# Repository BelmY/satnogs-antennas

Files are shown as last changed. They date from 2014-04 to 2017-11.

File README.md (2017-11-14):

# SatNOGS Antennas

Antennas for SatNOGS project

More information can be found in our [documentation](https://satnogs.org/documentation/hardware/).

## What's here?

### Helical antenna designs

* `Helical/UHC lhcp-version_1` is version 1 of our Helical antenna design.  It's
  a left-hand circularly polarized (LHCP) antenna, and requires only
  3D-printed parts (no CNC milling or laser-cutting required).

* `Helical/UHF-434-8-version_4` is version 4 of our Helical antenna design, an
  8-turn Helix that can be made in either left- or right-hand
  circularly polarized (RHCP) configurations.  It requires a laser cutter or
  water jet cutter for the plexiglass/polycarbonate supports, but is
  more rigid than version 1.

* `Helical/UHF-435-8-version_5` is version 5 of the Helical antenna
  design; it comes in RHCP configuration.  The supports are made from
  aluminum, and will require a drill press.

## License

&copy; 2014-2015 [Libre Space Foundation](http://librespacefoundation.org).

Licensed under the [CERN OHLv1.2](LICENSE).

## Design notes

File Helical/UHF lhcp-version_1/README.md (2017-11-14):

Documentation
====
Documentation and step by step building guide can be found in our [OHAI guide](https://ohai.satnogs.org/project/helical-antenna-v1/hardware/).

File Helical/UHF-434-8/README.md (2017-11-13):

# Helical Antenna v4

What's here:

* Summary files for RHCP antenna in stl and dxf format
  * Helical-434-8-RHCP.stl
  * Helical-434-8-RHCP.dxf

* Summary files for LHCP antenna in stl and dxf format
  * Helical-434-8-LHCP.stl
  * Helical-434-8-LHCP.dxf

* Printable blueprint file for RHCP in dxf and pdf format
  * Helical-434-RHCP-printBase.dxf
  * Helical-434-RHCP-printBase.pdf

* Printable blueprint file for LHCP in dxf and pdf format
  * Helical-434-LHCP-printBase.dxf
  * Helical-434-LHCP-printBase.pdf

* 6 radial base file for plexiglass or polycarbonate base in dxf and pdf format
  * Helical-434-6radialBase.dxf
  * Helical-434-6radialBase.pdf

* Plexiglass or polycarbonate triangular connector files
  * Helical-434-Triangle.dxf
  * Helical-434-Triangle.pdf

* Cooper matching triagle
  * Helical-434-CooperTriangle.dxf
  * Helical-434-CooperTriangle.pdf

* Dimensions table
  * Helical-434-8.xls

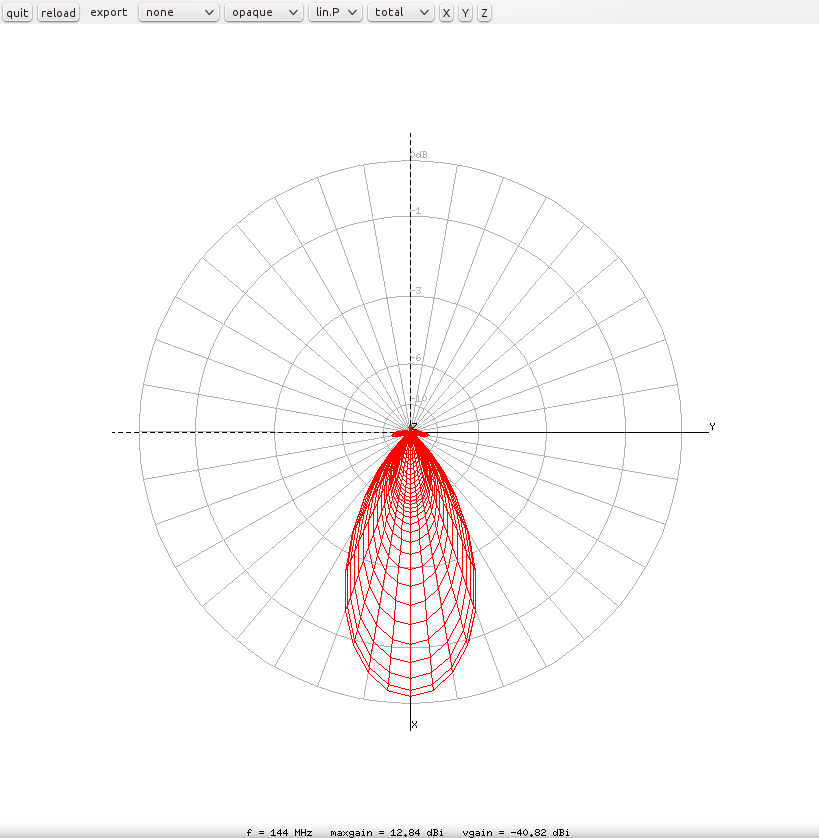
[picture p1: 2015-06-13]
NEC/SatNOGS 6-element - Radiation pattern.png

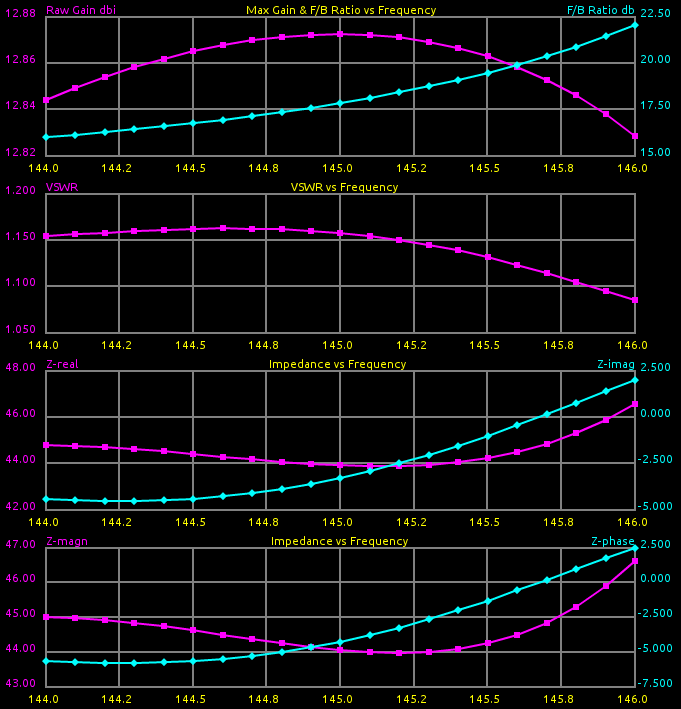
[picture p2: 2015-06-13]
NEC/SatNOGS 6-element - Gain_SWR_Impedance.png

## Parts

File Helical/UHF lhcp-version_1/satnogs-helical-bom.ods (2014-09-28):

Category | Description | Source | Qty | UOM | Estimated Price per Unit | Total Price | Comments
Mechanical | Galvanized Steel Wire 2mm |  | 10 | m | 0.2 | 2
Mechanical | Φ16 PVC Pipe |  | 6 | m | 1 | 6 | Condur Heavy Type
Mechanical | Galvanized Steel Grid 0.5x0.5'' 1mm |  | 0.16 | sqm | 8 | 1.28
Mechanical | Brass metal sheet 1.2mm |  | 0.45 | kg | 9 | 4.05 | We only need an orthogonal metal triangle of 204x41mm dimensions
Mechanical | M3 x 10mm |  | 0.02 | ea | 2 | 0.04
Mechanical | N-type Connector for case |  | 1 | ea | 4 | 4
Mechanical | M3 nut |  | 2 | ea | 0.01 | 0.02
Mechanical | M4 washer |  | 2 | ea | 0.02 | 0.04 | Enough big to be bigger than the grid square
Printed | T-Connector | Helix437-8r3-T.stl | 9 | ea | 0 | 0 | 3D printed, you can also use a finer design (check drawing)
Printed | Y-Connector | Helix437-8r3-Y.stl | 2 | ea | 0 | 0 | 3D printed, you can also use a finer design (check drawing)
Printed | YO-Connector | Helix437-8r3-YO.stl | 1 | ea | 0 | 0 | 3D printed, you can also use a finer design (check drawing)
 |  |  |  |  |  | 17.43

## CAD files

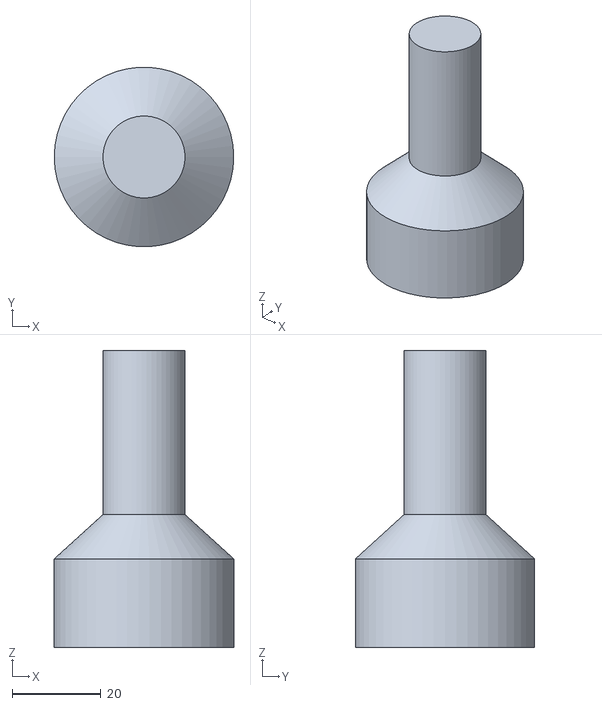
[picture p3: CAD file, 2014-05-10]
Turnstile/SatNOGS-turnstile-mount.stl
40.5 x 40.4 x 67.0

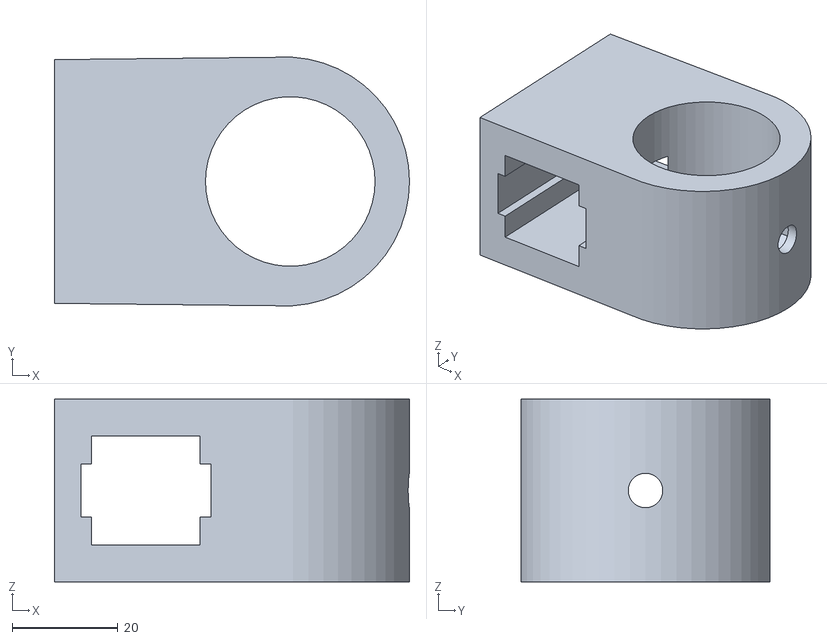
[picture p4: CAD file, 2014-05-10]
Yagi/Cross-Yagi-UHF-v1/satnogs-antenna-axis-mount-v2.stl
67.0 x 46.9 x 34.5

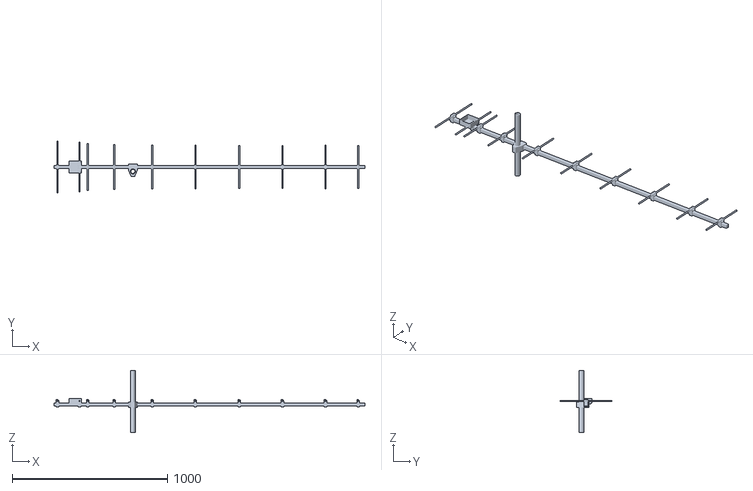
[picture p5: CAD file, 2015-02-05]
Yagi/Yagi-UHF-v1/435MHz-10EL8mm-2m-50-Ohm-Yagi.stl
2006.0 x 333.0 x 400.0

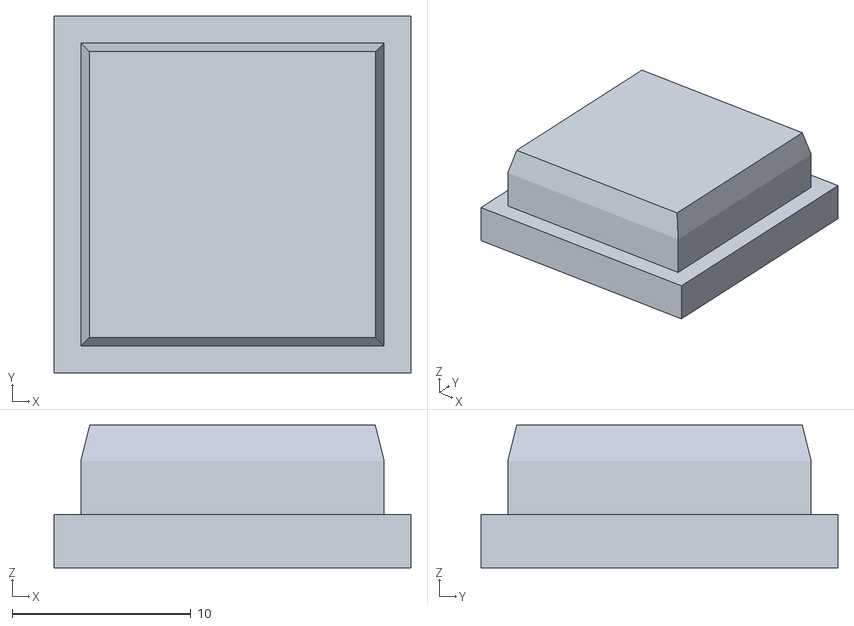
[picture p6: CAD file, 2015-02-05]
Yagi/Yagi-VHF-v3/Boom-cap.stl
20.0 x 20.0 x 8.00

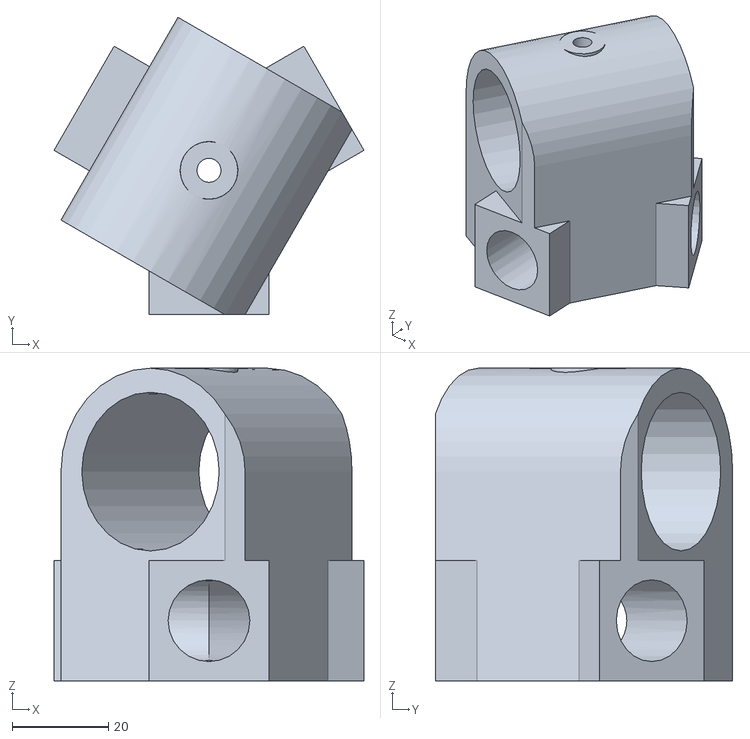
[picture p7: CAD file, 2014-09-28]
Helical/UHF lhcp-version_1/Helix437-8r3-YO.stl
64.5 x 61.8 x 65.0

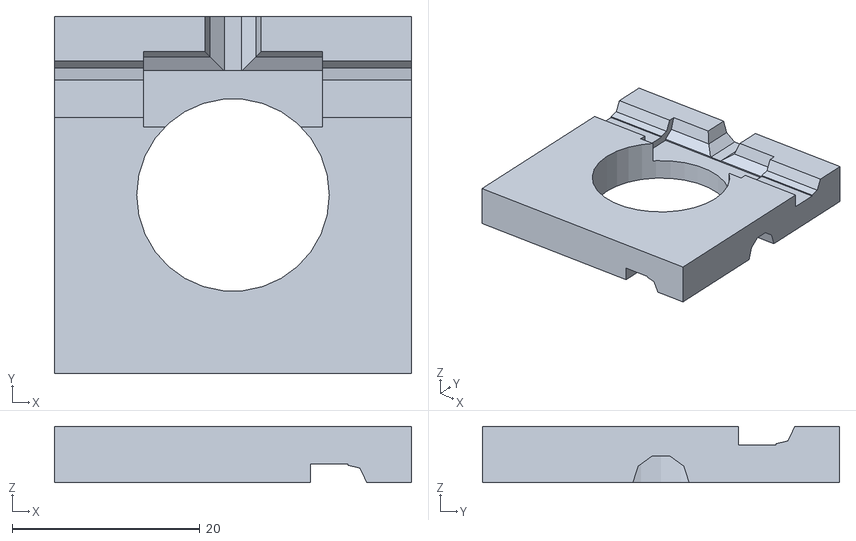
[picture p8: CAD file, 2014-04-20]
Yagi/Cross-Yagi-UHF-v1/satnogs-radiator-holder-middle.stl
38.0 x 38.0 x 6.00

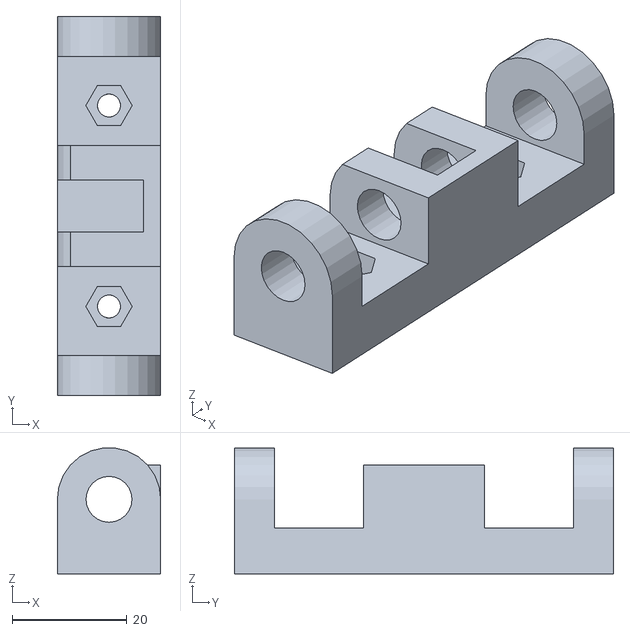
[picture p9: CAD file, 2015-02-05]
Yagi/Yagi-UHF-v1/El-middle435.stl
18.0 x 66.0 x 21.9

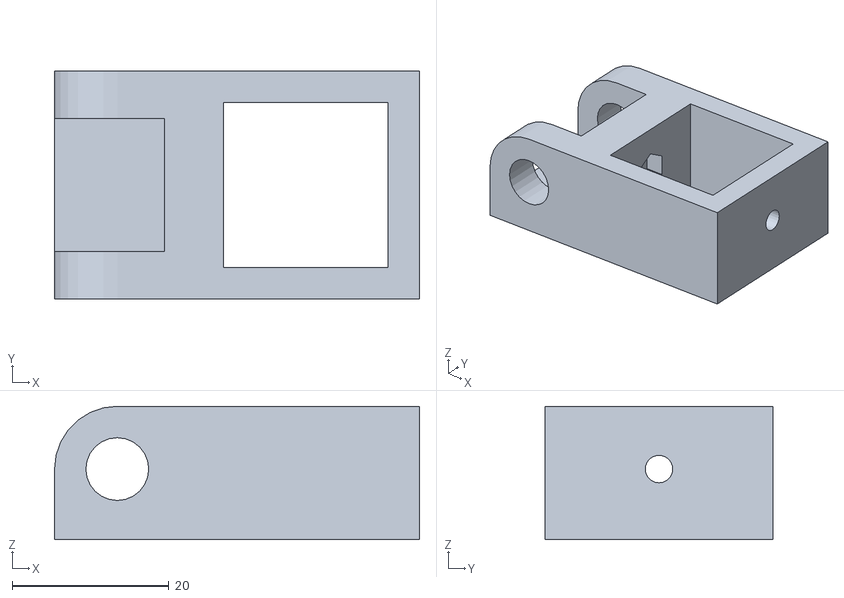
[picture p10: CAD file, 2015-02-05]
Yagi/Yagi-VHF-v3/El-conn.stl
46.5 x 29.0 x 17.0

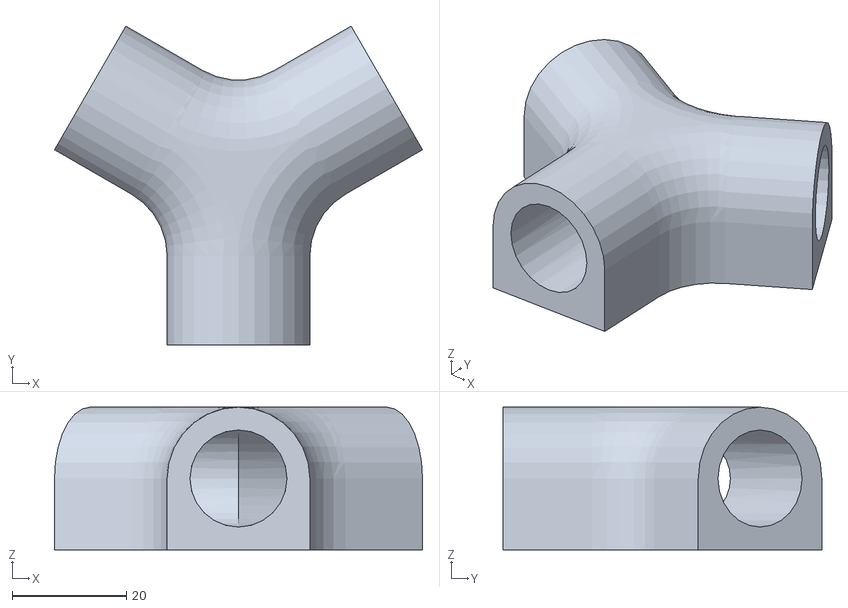
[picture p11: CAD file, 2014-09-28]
Helical/UHF lhcp-version_1/Helix437-8r3-Y.stl
64.5 x 55.8 x 25.0

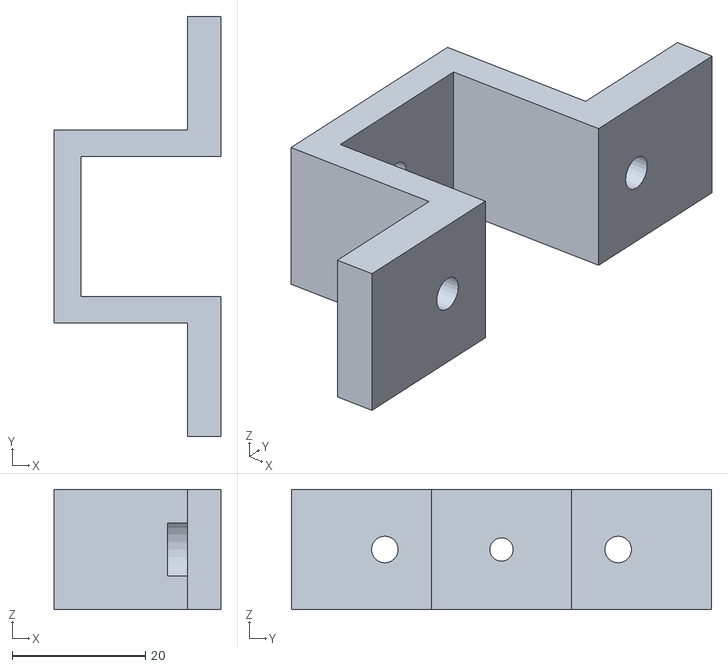
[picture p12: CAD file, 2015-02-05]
Yagi/Yagi-UHF-v1/omega435.stl
25.0 x 63.0 x 18.0

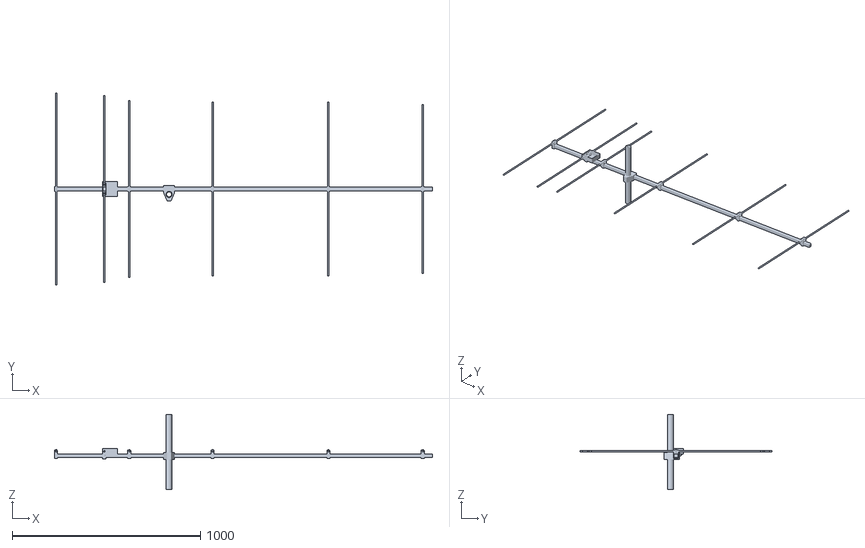
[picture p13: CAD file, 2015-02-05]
Yagi/Yagi-VHF-v3/145MHz-6EL8mm-2m-50-Ohm-Yagi.stl
2009.0 x 1020.0 x 400.0

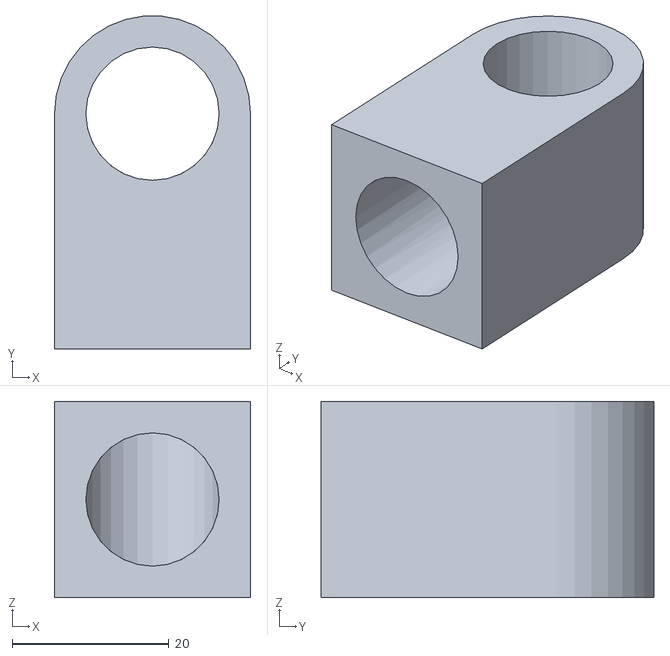
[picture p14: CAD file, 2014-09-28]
Helical/UHF lhcp-version_1/Helix437-8r3-T.stl
25.0 x 42.4 x 25.0

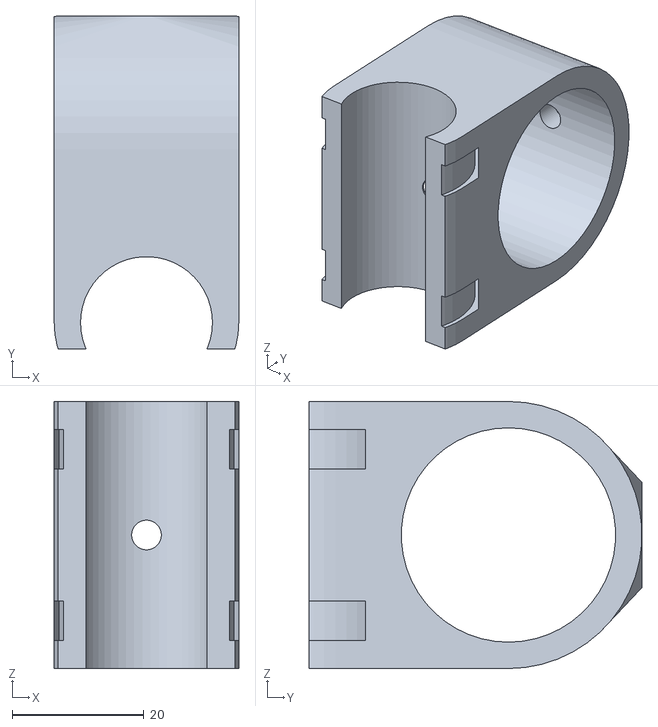
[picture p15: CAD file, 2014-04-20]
Yagi/Cross-Yagi-UHF-v1/satnogs-antenna-axis-mount-single-pole.stl
28.0 x 50.5 x 40.5

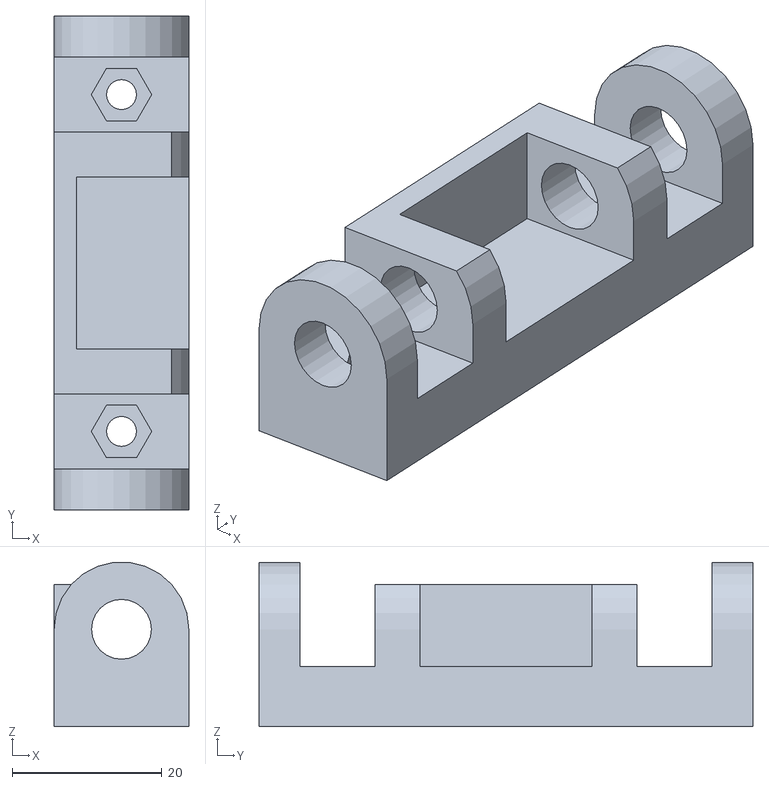
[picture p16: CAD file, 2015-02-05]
Yagi/Yagi-VHF-v3/El-middle145.stl
18.0 x 66.0 x 21.9

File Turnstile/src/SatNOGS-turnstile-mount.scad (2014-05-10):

// SatNOGS Turnstile antenna mount

$fn=50;

// Variables
i_b = 32.5; //Inner Bottom width
o_u = 18.5; //Outer Upper width
t_h = 10; //Transitional height

// Main model

module mount(){
	difference(){
		union(){
			translate([0,0,-10])
				cylinder(d=i_b+8, h=20, center=true);
			translate([0,0,t_h/2])
				cylinder(d1=i_b+8, d2=o_u, h=t_h, center=true);
			translate([0,0,t_h+(o_u*2)/2])
				cylinder(d=o_u, h=o_u*2, center=true);
		}
		translate([0,0,-11])
			cylinder(d=i_b, h=22, center=true);
	}
}

mount();

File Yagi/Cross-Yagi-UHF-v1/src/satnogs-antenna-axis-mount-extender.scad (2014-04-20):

// Antenna to axis mount
// Satnogs Project 2014 MPL2.0 http://satnogs.org

$fn=50;

mast_1 = 32;		 // Axis mast diameter
mast_2 = 20;		 // Antenna mast diameter
offset = 8;			 // Extra width of mount
tireup_w = 6; 		 // Width of tireup
tireup_h = 1.5;	 // Height of tireup
washer = 16;		 // Washer diameter
bolt = 4;			 // Bolt for antenna mast


module axises() {
	translate([0,(mast_1+mast_2)/2-mast_1/2,0])
		rotate([0,90,0])
			cylinder(h=mast_2+offset+1, d=mast_1, center=true);
	translate([0,-(mast_1+mast_2)/2+mast_2/2,0])
		cylinder(h=mast_1+offset+1, d=mast_2, center=true);
	// Bolt for antenna mast cylinder
	translate([0,(mast_1+mast_2)/2-mast_1/2,0])
		cylinder(h=mast_1+offset+1, d=bolt, center=true);
}

module axises_outer() {
	translate([0,(mast_1+mast_2)/2-mast_1/2,0])
		rotate([0,90,0])
			cylinder(h=mast_2+offset, d=mast_1+offset, center=true);
	translate([0,-(mast_1+mast_2)/2+mast_2/2,0])
		cylinder(h=mast_1+offset, d=mast_2+offset, center=true);
	// Outer washer stud
	translate([0,(mast_1+mast_2)/2-mast_1/2,0])
		cylinder(h=mast_1+offset, d=washer, center=true);
}

module tire_up() {
	difference() {
		cylinder(h=tireup_w,d=mast_2+offset+tireup_h,center=true);
		cylinder(h=tireup_w,d=mast_2+offset-tireup_h,center=true);
	}
}

module cut() {
	translate([0,-(mast_1+mast_2)/2,0])
		cube([offset*5,offset*1.5,mast_1+offset*4],center=true);
}

module main_connector() {
	difference() {
		hull() {
			axises_outer();
		}
		axises();
		mirror([0,0,1]) {
			translate([0,-(mast_1+mast_2)/2+mast_2/2,(2*mast_1)/5])
				tire_up();
		}
		translate([0,-(mast_1+mast_2)/2+mast_2/2,(2*mast_1)/5])
			tire_up();
		cut();
	}
}

module extender() {
	difference() {
		translate([mast_1/2-offset/2,-mast_2*2,-mast_1/2-offset/4])
			cube([offset/2,mast_1*2,offset/2],center=true);
		translate([mast_1/2-offset/2,-mast_1*2-4,-mast_1/2-offset/4])
			cylinder(d=3,offset/2,center=true);
	}
}

difference() {
	union() {
		main_connector();
		extender();
	}
}

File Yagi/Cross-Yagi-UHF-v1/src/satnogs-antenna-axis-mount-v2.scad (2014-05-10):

// SatNOGS Yagi v2 Axis mount

//$fn = 20;

include <cyl_head_bolt.scad>;

// Variables

axis = 32; //Axis diameter
mast = 20.5; //Yagi width
w = 7; 	  //Mount wall width

module mount_outer(){
	union(){
		translate([axis/2+1,0,0])
			cylinder(d=axis+2*w,h=mast+2*w,center=true);
		translate([-mast/2,0,0])
			cube([mast+2*w,axis+2*w,mast+2*w],center=true);
	}
}

module mount_inner(){
	union(){
		translate([axis/2+1,0,0])
			cylinder(d=axis,h=mast+2*w+1,center=true);
		translate([-mast/2,0,0])
			cube([mast,axis+2*w+1,mast],center=true);
	}
}

module nutsbolts(){
	translate([-mast+1,0,0])
		rotate([0,90,0])
			nutcatch_parallel("M6", l=6);
	translate([-mast,0,0])
		rotate([0,90,0])
			cylinder(r=3.25,h=15,center=true);
	translate([axis+4,0,0])
		rotate([0,90,0])
			nutcatch_parallel("M6", l=8);
	translate([axis,0,0])
		rotate([0,90,0])
			cylinder(r=3.25,h=15,center=true);
}

module nipple_rail(){
	translate([-mast,0,0])
		cube([4,axis+2*w+1,10],center=true);
	cube([4,axis+2*w+1,10],center=true);
}

difference() {
	hull() {
		mount_outer();
	}
	mount_inner();
	nutsbolts();
	nipple_rail();
}

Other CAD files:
Helical/UHF lhcp-version_1/Helix437-8r3.dwg
Yagi/Yagi-UHF-v1/pipe-conn.stl
Yagi/Cross-Yagi-UHF-v1/src/satnogs-antenna-axis-mount-single-pole.scad
Helical/UHF lhcp-version_1/old/Helix437-8r1.dwg
Helical/UHF lhcp-version_1/old/Helix437-8r2.dwg
Helical/UHF-434-8-version_4/Helical-434-6radialBase.dxf
Helical/UHF-434-8-version_4/Helical-434-CooperTriangle.dxf
Helical/UHF-434-8-version_4/Helical-434-LHCP-printBase.dxf
Helical/UHF-434-8-version_4/Helical-434-RHCP-printBase.dxf
Helical/UHF-434-8-version_4/Helical-434-Triangle.dxf
Yagi/Cross-Yagi-UHF-v1/satnogs-antenna-axis-mount.stl
Yagi/Cross-Yagi-UHF-v1/satnogs-t-connector.stl
Yagi/Cross-Yagi-UHF-v1/satnogs-yagi-holder-4.5mm.stl
Yagi/Cross-Yagi-UHF-v1/satnogs-yagi-holder-4.stl
Yagi/Cross-Yagi-UHF-v1/satnogs-yagi-holder-5mm.stl
Yagi/Cross-Yagi-UHF-v1/satnogs-yagi-holder.stl
Yagi/Cross-Yagi-UHF-v1/src/satnogs-antenna-axis-mount.scad
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

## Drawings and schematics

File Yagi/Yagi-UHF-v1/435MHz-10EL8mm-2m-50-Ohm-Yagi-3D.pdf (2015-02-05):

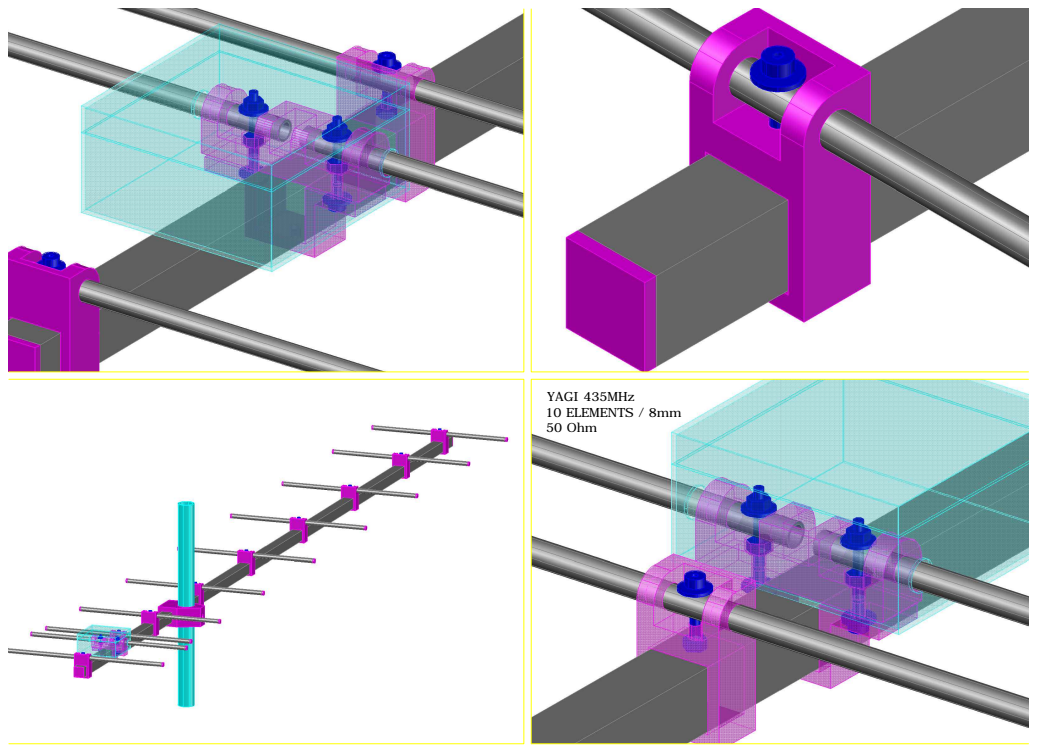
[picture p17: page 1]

YAGI 435MHz 10 ELEMENTS / 8mm 50 Ohm

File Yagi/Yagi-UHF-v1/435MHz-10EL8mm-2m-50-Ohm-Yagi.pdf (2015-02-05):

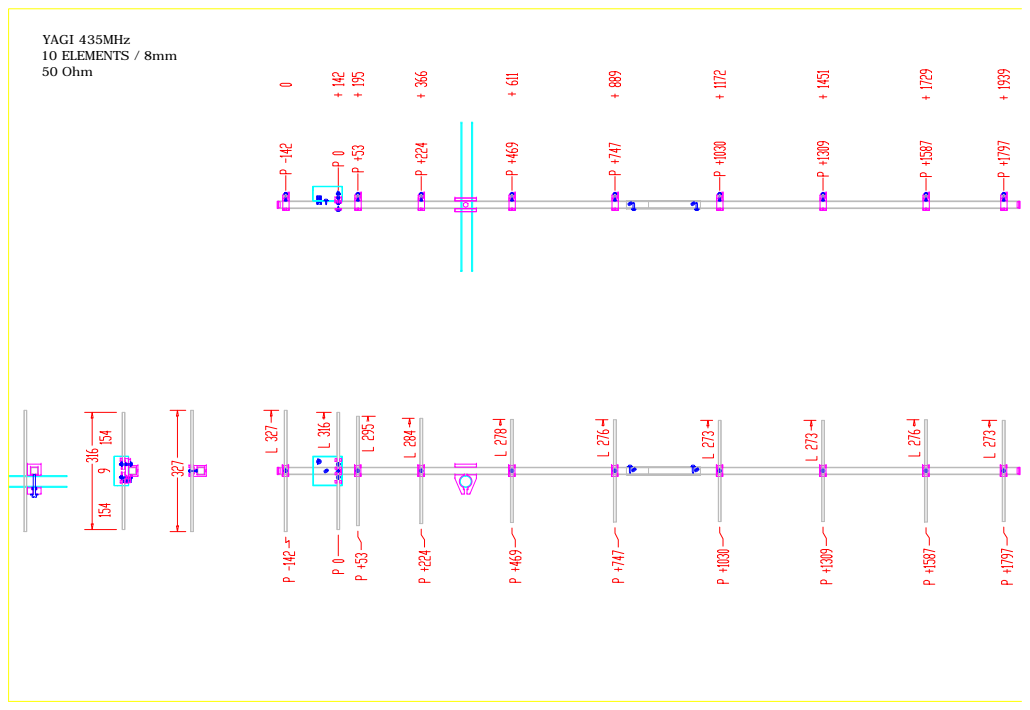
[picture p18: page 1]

YAGI 435MHz 10 ELEMENTS / 8mm 50 Ohm

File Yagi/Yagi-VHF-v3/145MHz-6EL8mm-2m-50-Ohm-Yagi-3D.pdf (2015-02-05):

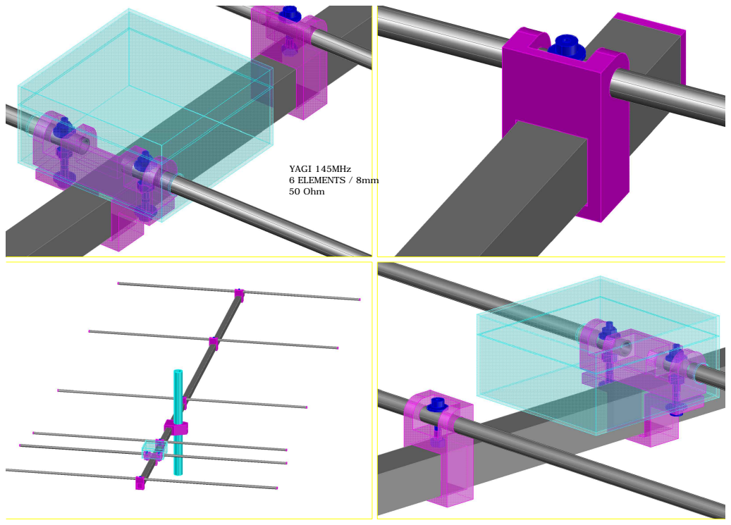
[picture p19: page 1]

YAGI 145MHz 6 ELEMENTS / 8mm 50 Ohm

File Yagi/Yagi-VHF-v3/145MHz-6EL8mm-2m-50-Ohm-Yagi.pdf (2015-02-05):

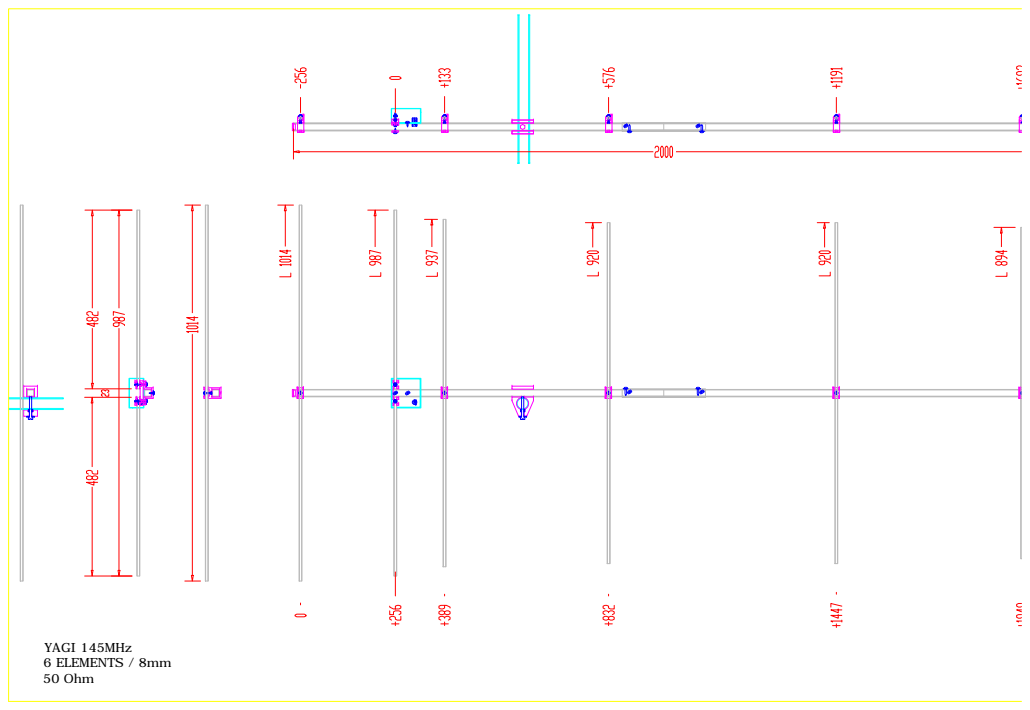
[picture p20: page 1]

YAGI 145MHz 6 ELEMENTS / 8mm 50 Ohm

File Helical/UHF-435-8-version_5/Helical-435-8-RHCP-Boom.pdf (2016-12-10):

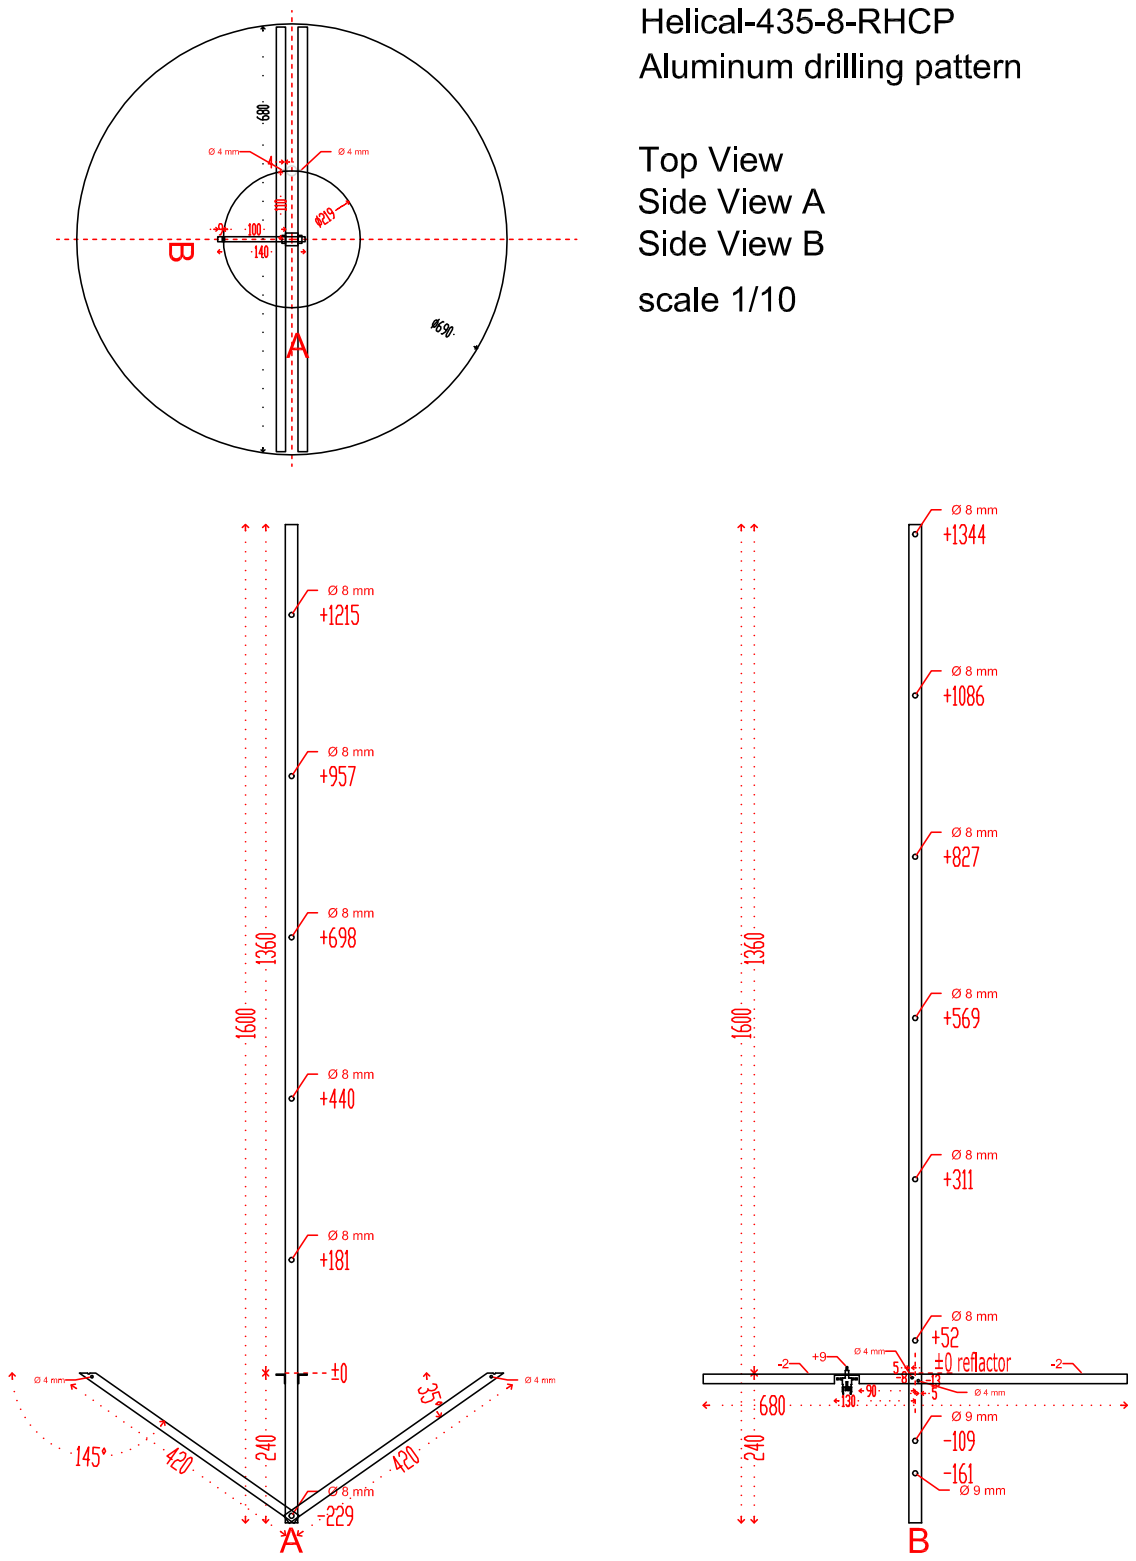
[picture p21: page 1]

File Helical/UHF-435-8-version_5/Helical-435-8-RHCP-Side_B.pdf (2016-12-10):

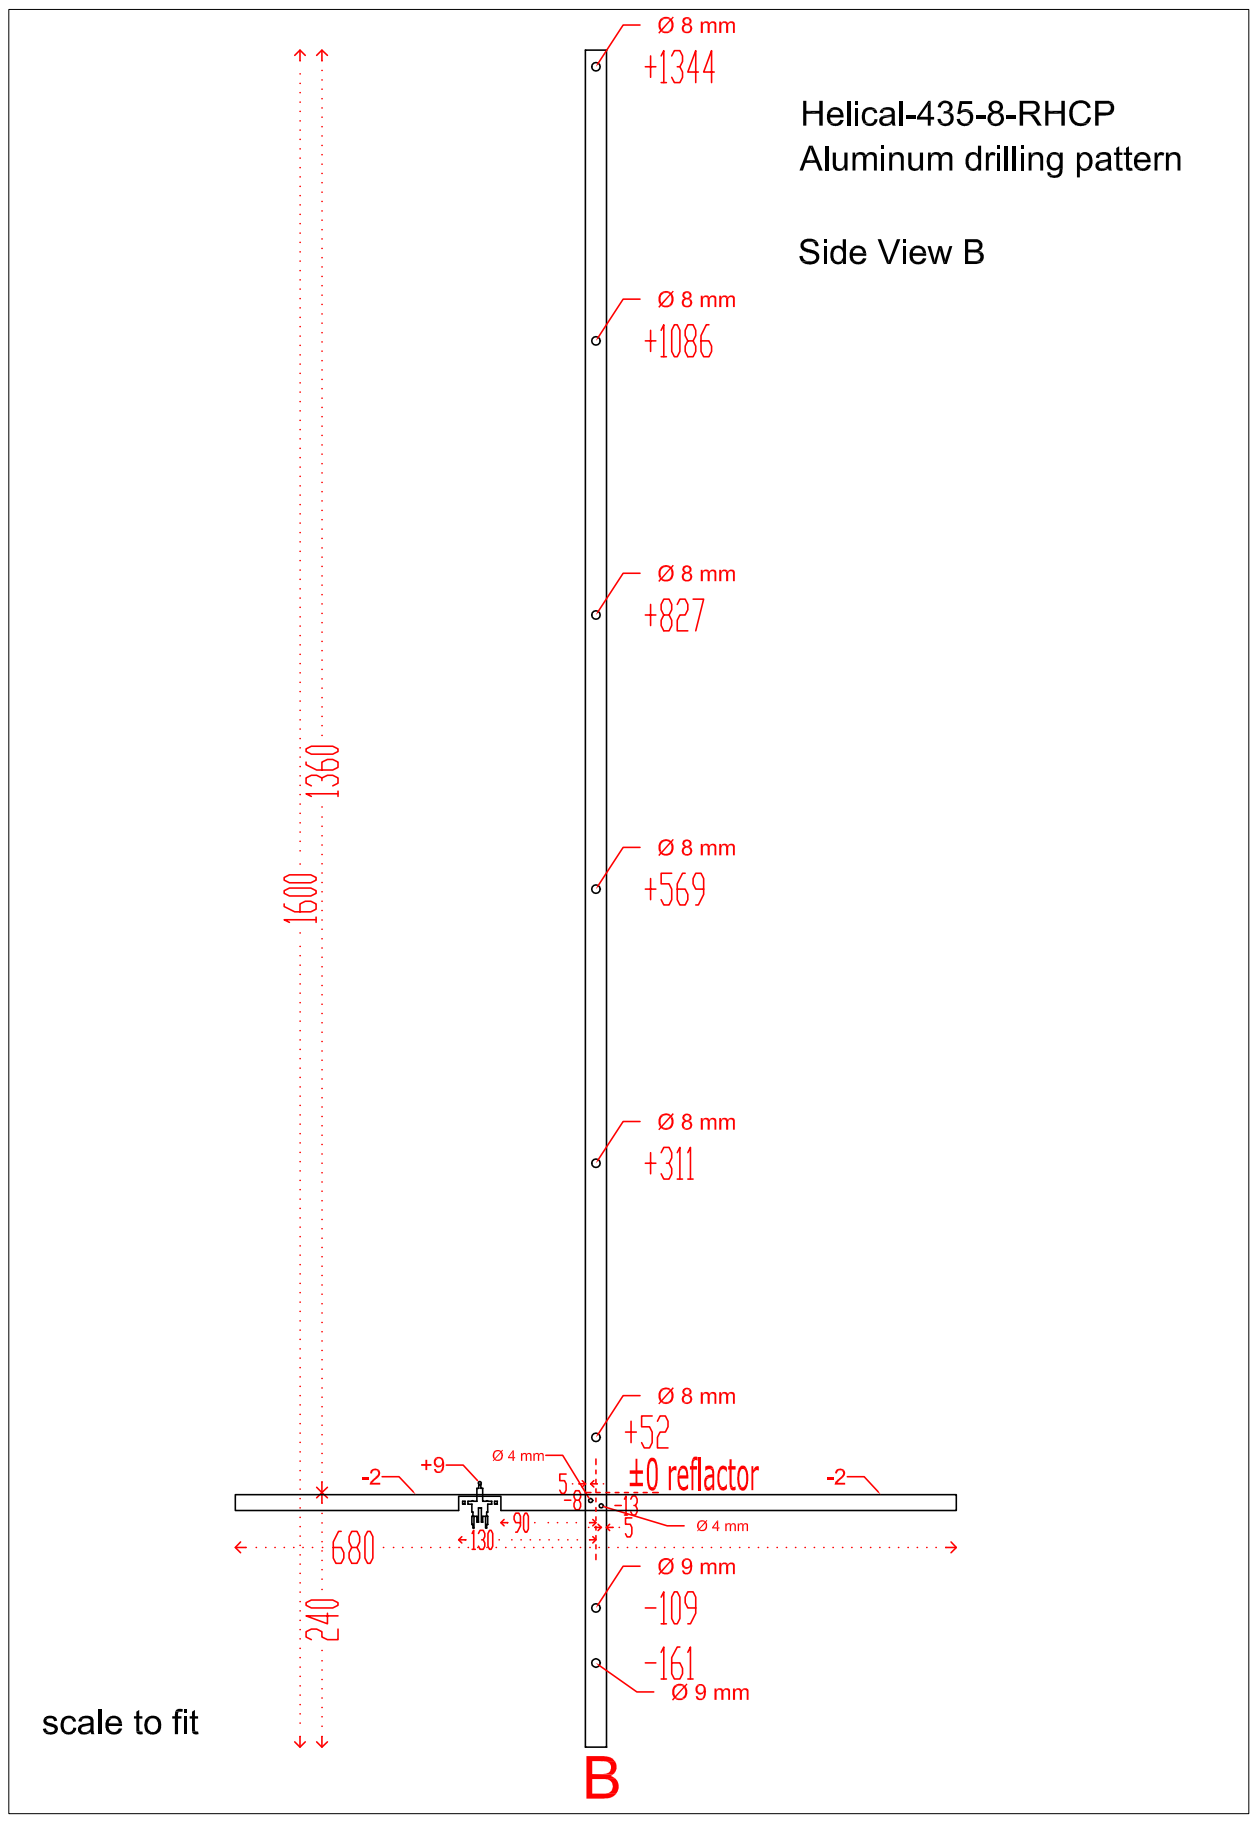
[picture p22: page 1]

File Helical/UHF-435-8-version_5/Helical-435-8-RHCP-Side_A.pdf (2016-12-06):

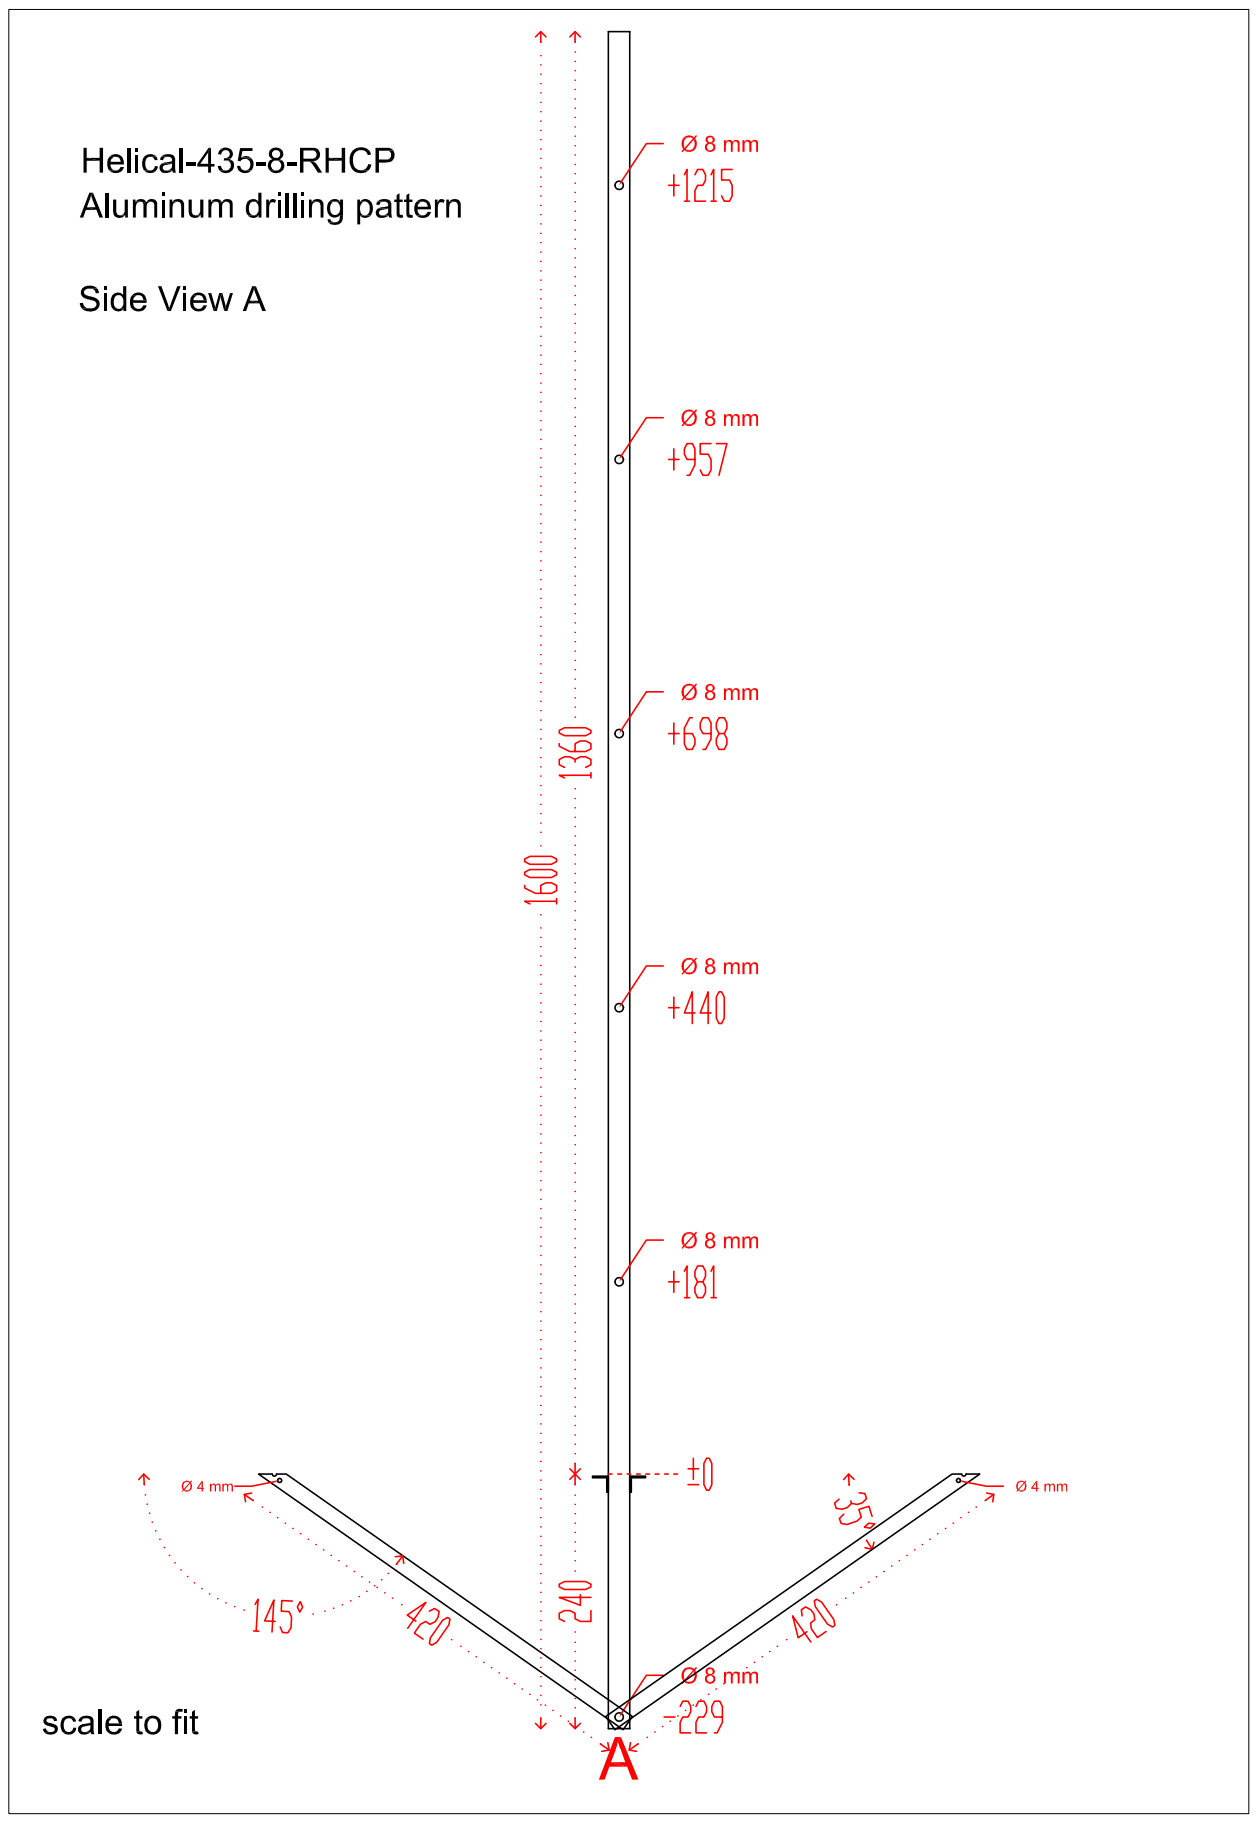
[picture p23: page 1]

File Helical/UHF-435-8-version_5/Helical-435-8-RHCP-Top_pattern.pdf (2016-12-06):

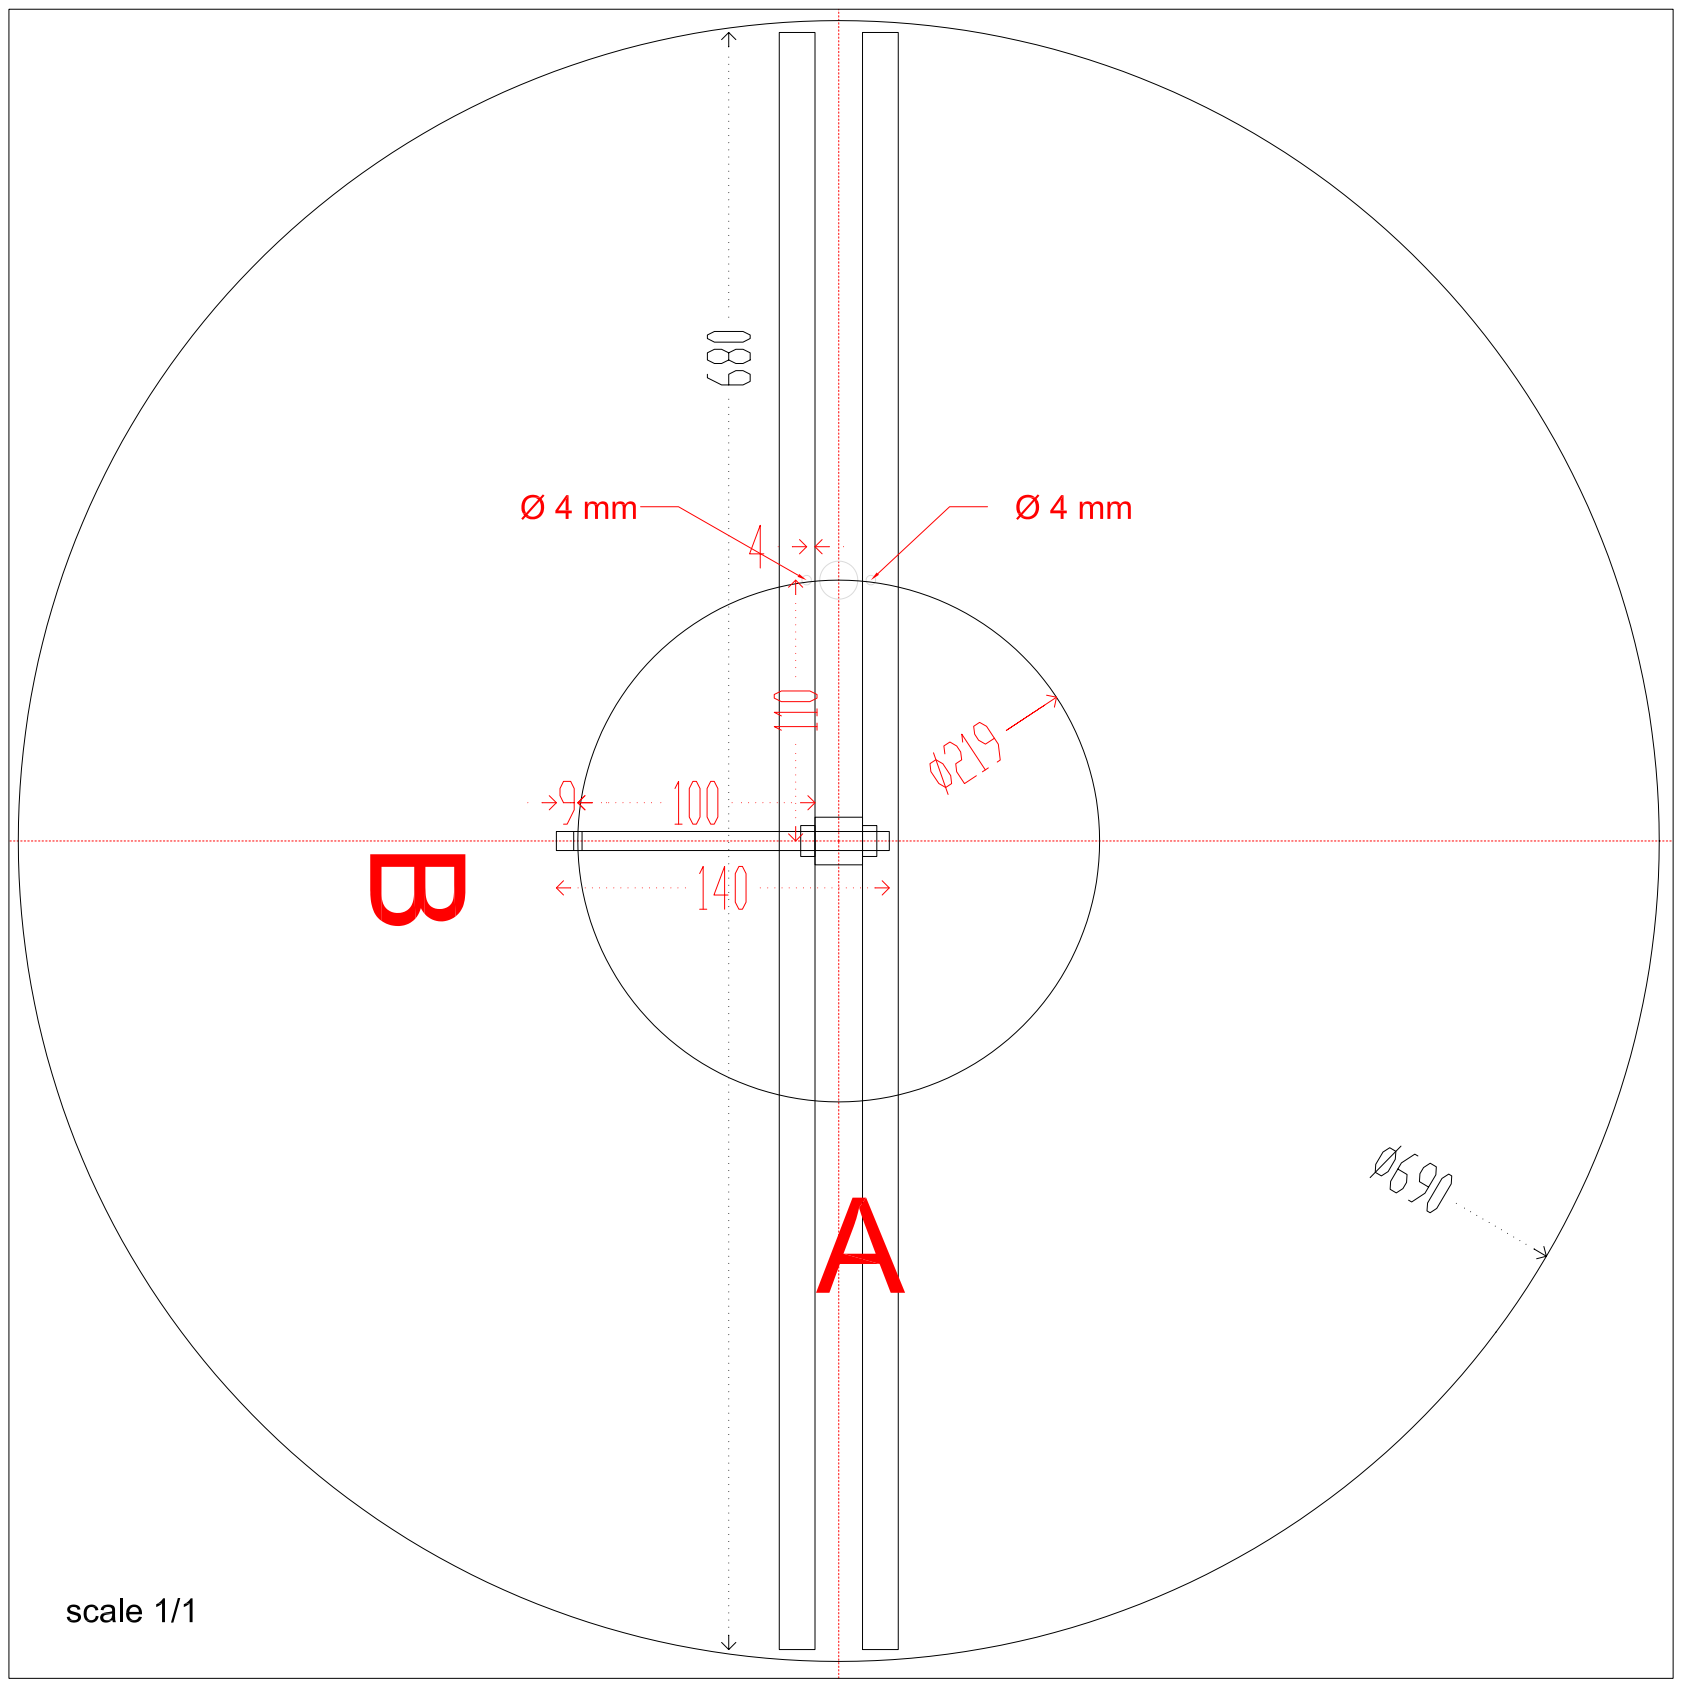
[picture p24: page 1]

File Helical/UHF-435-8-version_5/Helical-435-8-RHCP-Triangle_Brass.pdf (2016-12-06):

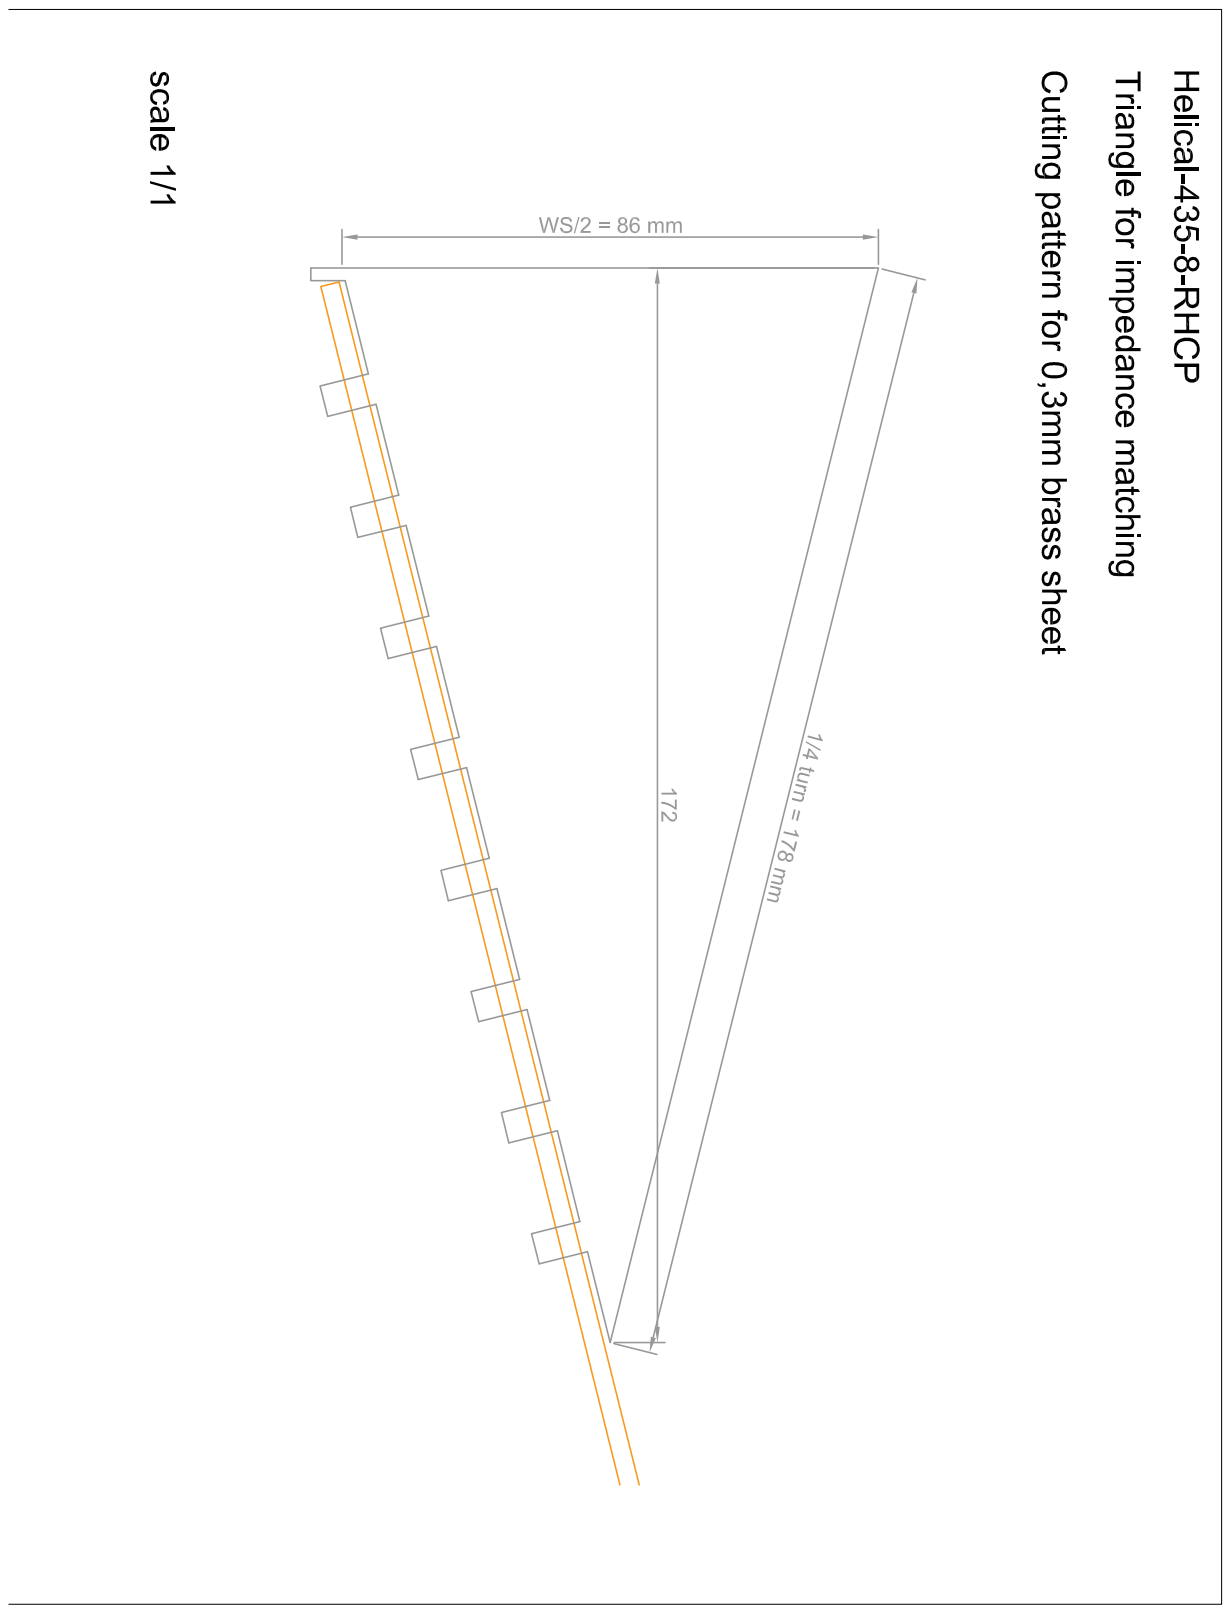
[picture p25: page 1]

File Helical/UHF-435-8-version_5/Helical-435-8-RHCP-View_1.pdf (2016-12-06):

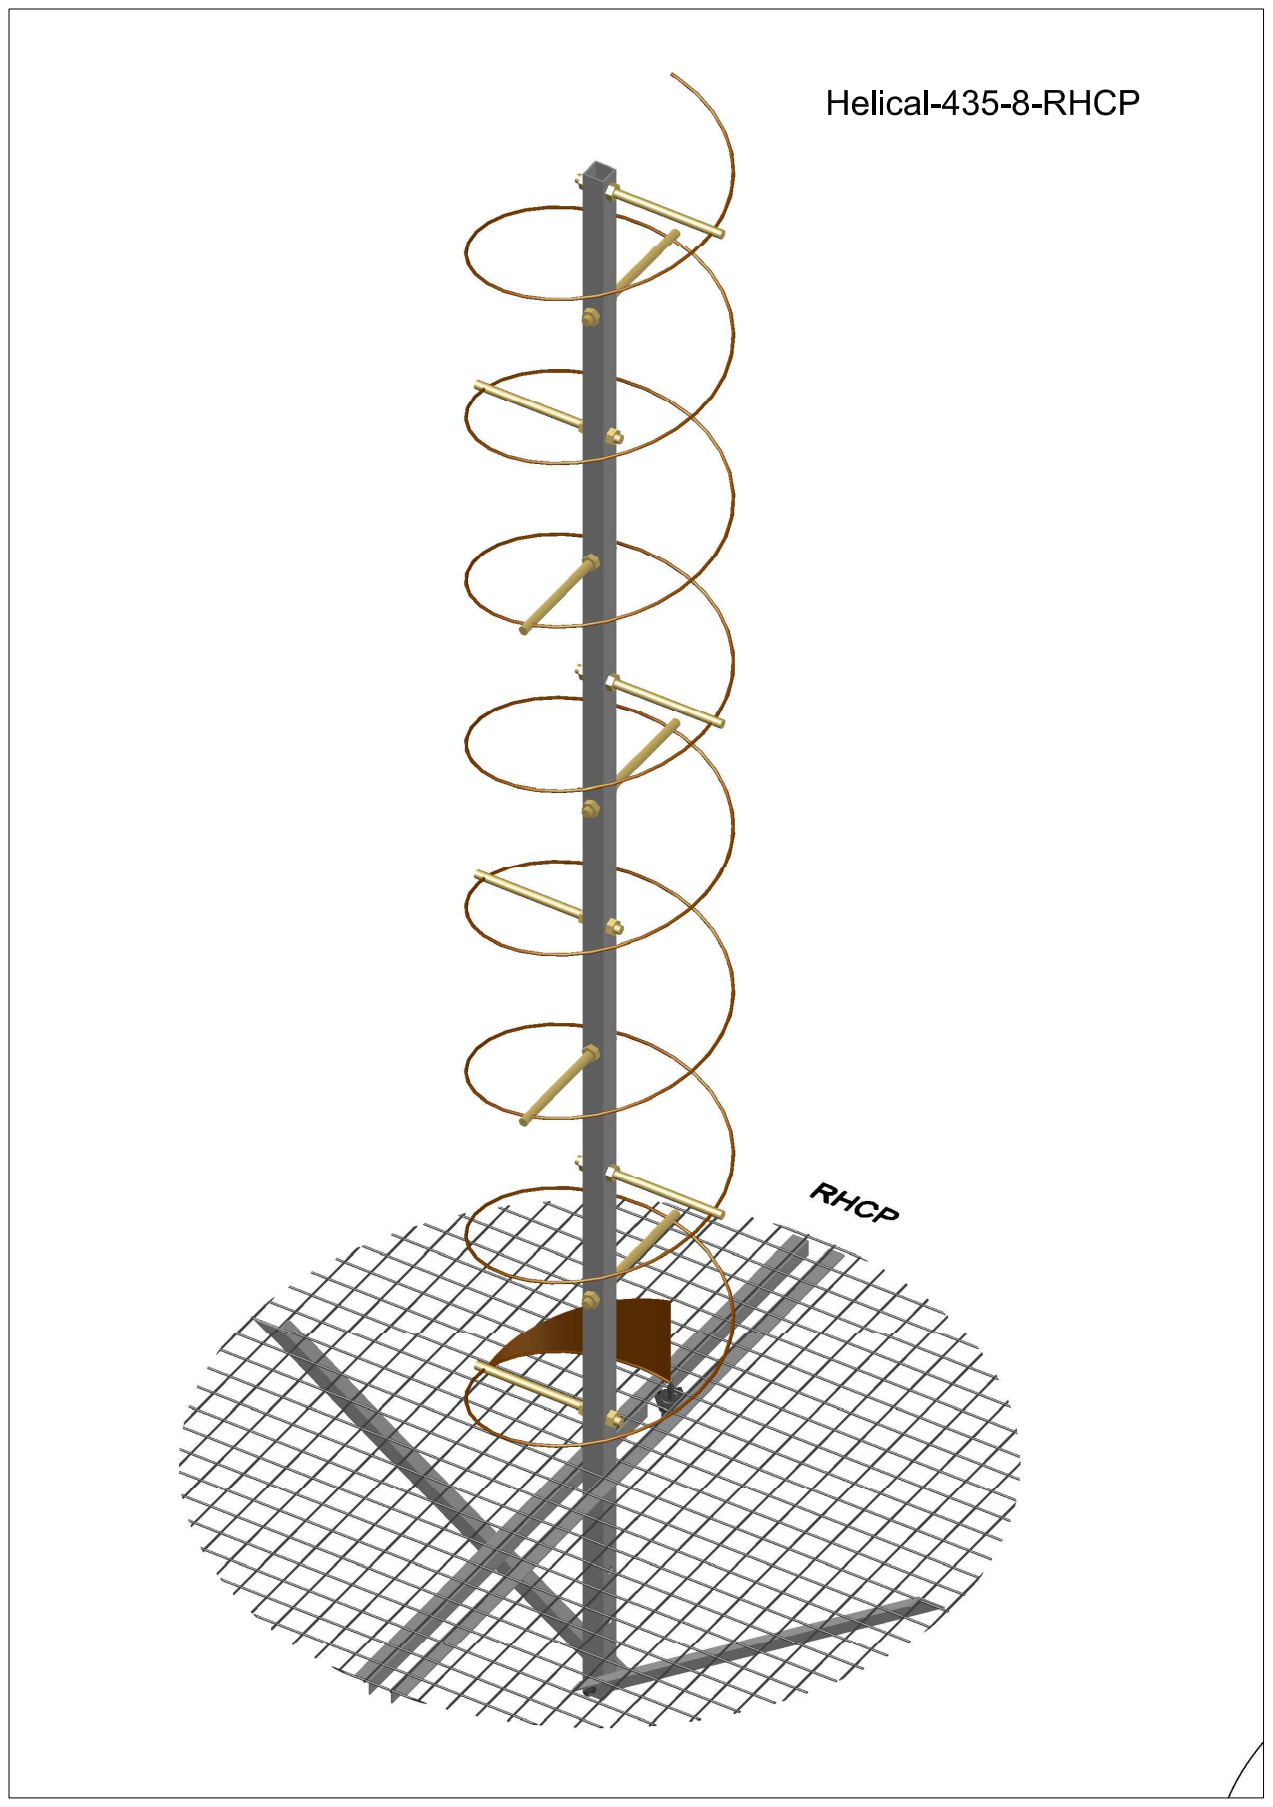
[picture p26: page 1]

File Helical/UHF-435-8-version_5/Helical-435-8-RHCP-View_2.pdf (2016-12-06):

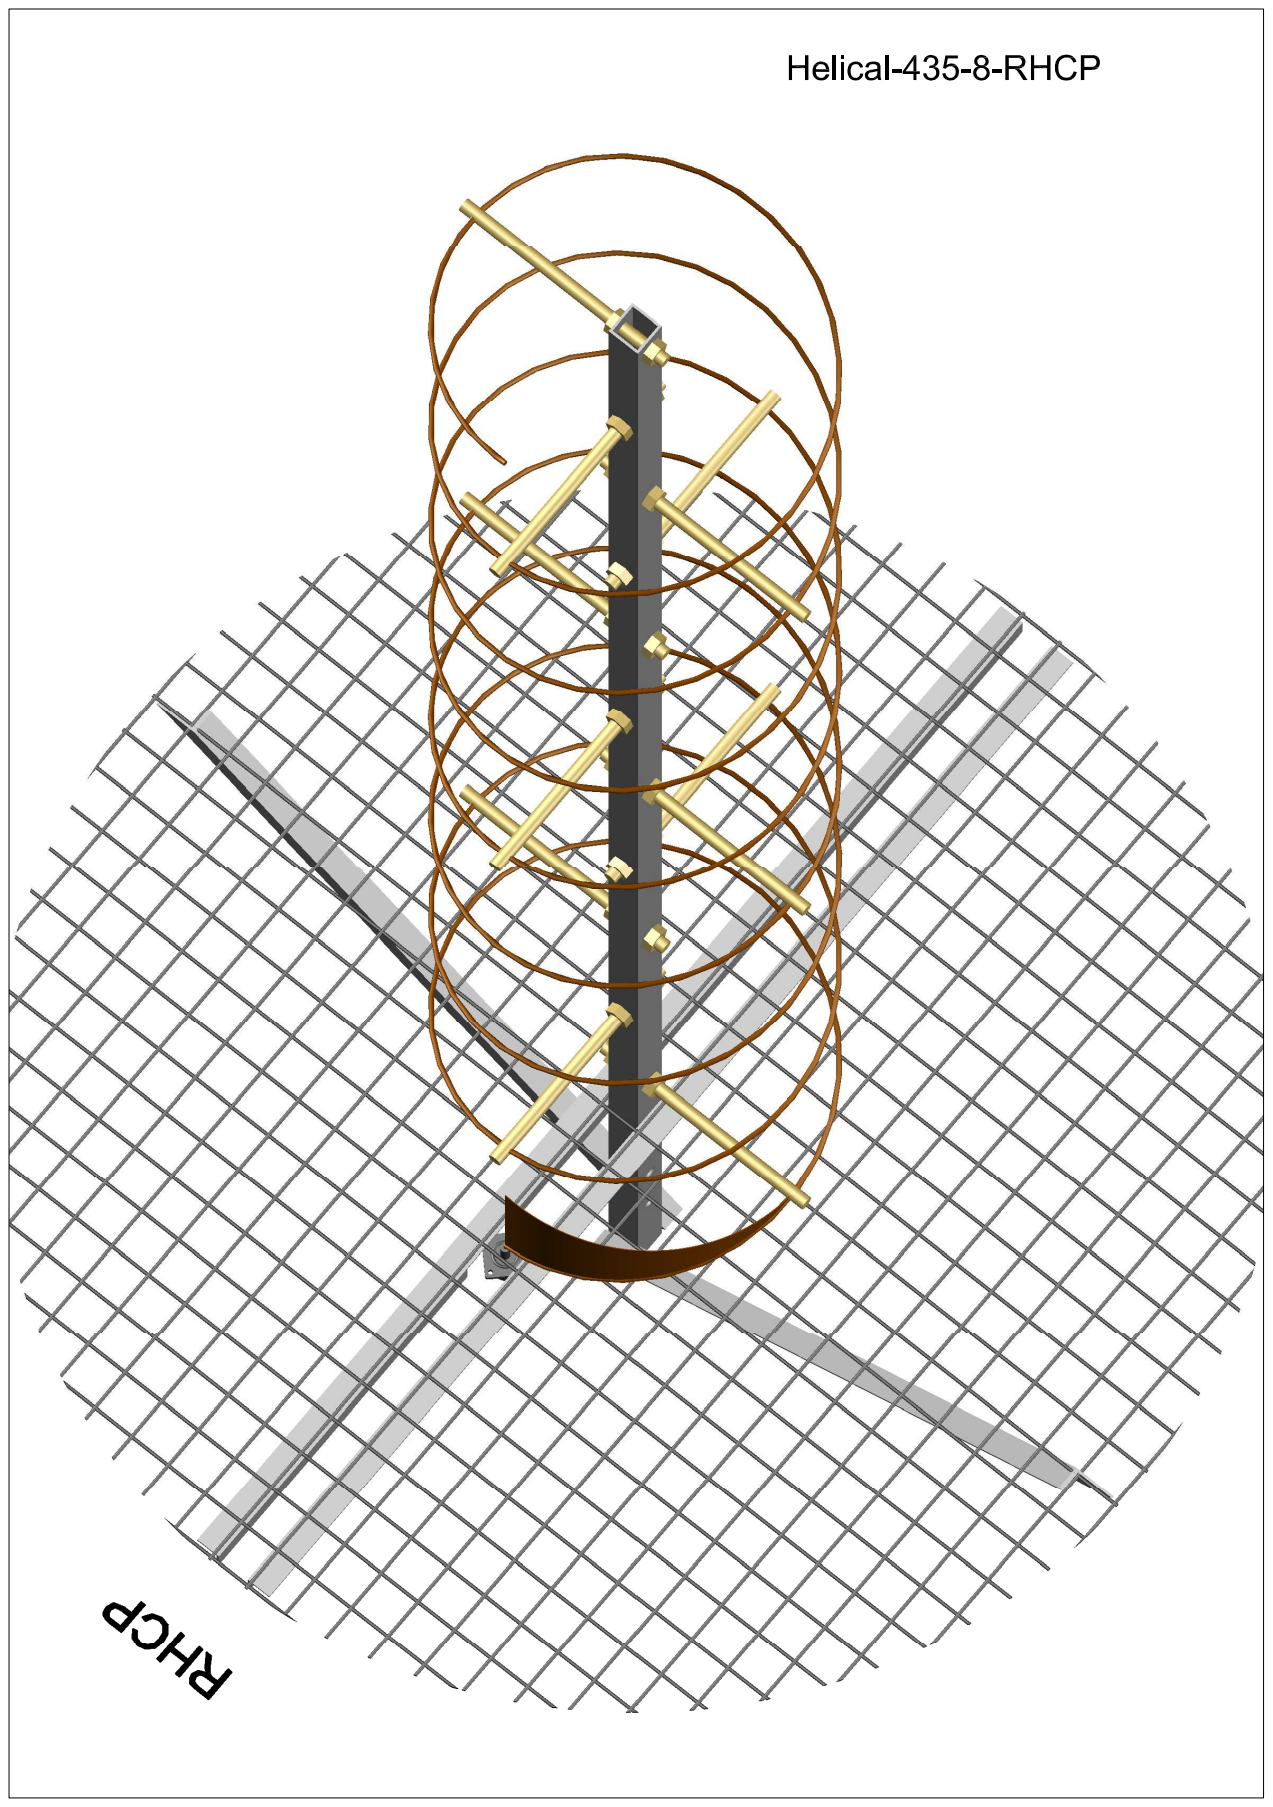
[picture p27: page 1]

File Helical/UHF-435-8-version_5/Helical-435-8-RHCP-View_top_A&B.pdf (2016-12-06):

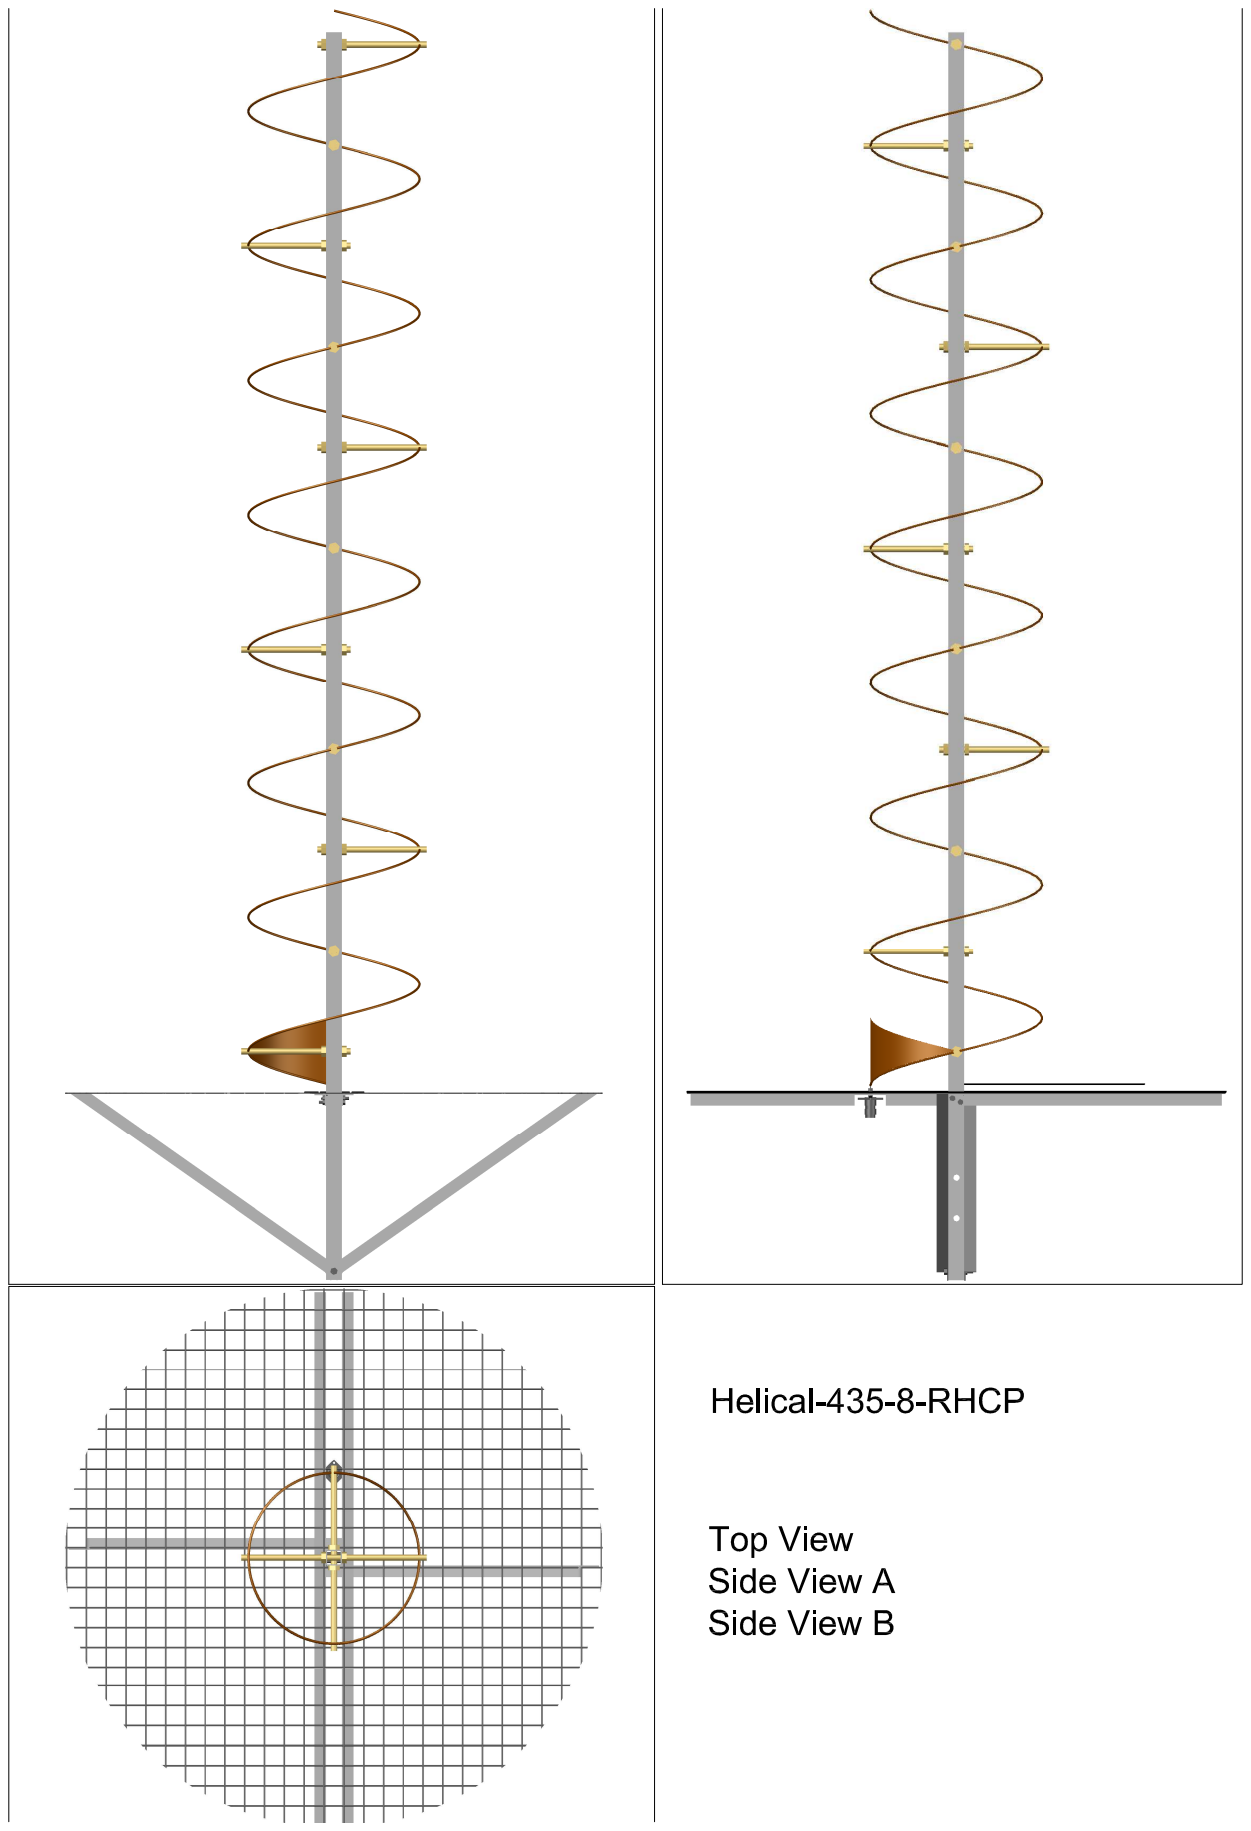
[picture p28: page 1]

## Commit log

2014-04-13 Yagi element to mast mounting bracket
    [satnogs-yagi-holder-5mm.stl, satnogs-yagi-holder.scad, satnogs-yagi-holder.stl]
2014-04-13 Code clean up and new stls
    [satnogs-yagi-holder-4.5mm.stl, satnogs-yagi-holder-4.stl, satnogs-yagi-holder.scad]
2014-04-13 T-connector and refactored code for axis mount
    [satnogs-antenna-axis-mount.scad, satnogs-antenna-axis-mount.stl, satnogs-t-connector.scad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]
2014-04-13 STL files of the tracking box system.
    [axis large.stl, axis small.stl, azimouth spacer.stl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]
2014-04-15 made axis hole smaller and added holes for screws
    [axis large.stl]
2014-04-15 added box axis bushing file
    [box axis bushing.stl]
2014-04-15 corrected axis bushing file to fit in box
    [box axis bushing.stl]
2014-04-15 enlarged bushing and axis large axis diameter
    [axis large.stl, box axis bushing.stl]
2014-04-20 Tripod and yagi antenna holders
    [satnogs-antenna-axis-mount-extender.scad, satnogs-antenna-axis-mount-single-pole.scad, satnogs-antenna-axis-mount-single-pole.stl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]
2014-04-22 Add assemply blender filles .gitignore and how to blend and pics
    [azimuth spacer.stl]
2014-04-23 added antenna axs joint.stl file
    [antenna axis joint.stl]
2014-05-10 New antenna axis mount
    [cyl_head_bolt-drawAllScript.scad, cyl_head_bolt.scad, data-access.scad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]
2014-05-10 Manifold fix
    [satnogs-antenna-axis-mount-v2.scad, satnogs-antenna-axis-mount-v2.stl]
2014-05-10 Turnstile antenna mount
    [SatNOGS-turnstile-mount.scad, SatNOGS-turnstile-mount.stl]
2014-08-20 v0.1 source initial and final commit
    [antenna axis joint.fcstd, base.fcstd, cross.fcstd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]
2014-08-20 v0.2 source initial commit
    [base.fcstd, gear.fcstd, nema17stepper.fcstd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]
2014-08-20 LNA housing
    [lna-housing-down.stl, lna-housing-up.stl, lna-housing.scad]
2014-08-20 Fixing spelling
    [lna-housing-down.stl, lna-housing-up.stl, lna-housing.scad]
2014-09-24 Ground Station Tracking v2
    [antenna axis joint.fcstd, antenna axis joint.stl, axis large.stl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]
2014-09-24 Update BOM with links to STLs.
    [santogs-mechanical-bom.ods, satnogs-mechanical-bom.ods]
2014-09-24 Update Antenna directories.
    [SatNOGS-turnstile-mount.scad, SatNOGS-turnstile-mount.stl, cyl_head_bolt-drawAllScript.scad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]
2014-09-24 Updated BOM.
    [homing_ring.stl, satnogs-mechanical-bom.ods]
2014-09-28 New Helical antenna UHF lhcp.
    [Helix437-8r1.dwg, Helix437-8r2.dwg, Helix437-8r3-T.stl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]
2014-09-28 Add BOM of helical antenna UHF-lhcp.
    [satnogs-helical-bom.ods]
2014-09-29 Add v2 of Tripod.
    [SatNOGS-3pod - 21r-bottom.stl, SatNOGS-3pod - 21r-top.stl, SatNOGS-3pod - 21r.dwg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]
2014-10-04 Add axis_bushing source file.
    [axis_bushing.fcstd, axis_bushing.stl]
2014-10-04 Add Axis Gear Spacer for v2.
    [axis_gear_spacer.fcstd, axis_gear_spacer.stl, satnogs-mechanical-bom.ods]
2014-10-22 Add BOM for tripod v2
    [satnogs-tripod-v2-bom.ods]
2014-10-24 Radome v1 added.
    [3V-6_8-a.stl, 3V-6_8-b.stl, 3V-6_8-c.stl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]
2014-10-26 Add all files for the diplexer schematic and pcb design
    [Diplexer.brd, Diplexer.sch, Diplexer_HPF.sch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]
2014-10-27 Add Diplexer BOM.
    [diplexer_bom.ods]
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2014-10-27 Add Radome BOM.
    [satnogs-radome-v1-bom.ods]
2014-10-28 Update trakcer BOM.
    [satnogs-mechanical-bom.ods]
2015-01-09 Add pockets for nuts at the axis_side part and update the stl file to
    [axis_side.fcstd, axis_side.stl]
2015-01-18 Adding new yagi VHF v2
    [145MHz-6-Element-2m-50-Ohm-Yagi.dwg, 145MHz-6-Element-2m-50-Ohm-Yagi.stl, 145MHz-6-Element-cap.stl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]
2015-02-05 New VHF v3 6element design.
    [145MHz-6EL8mm-2m-50-Ohm-Yagi.dwg, 145MHz-6EL8mm-2m-50-Ohm-Yagi.stl, Boom-cap.stl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]
2015-02-05 New UHF v1 10 elements design.
    [435MHz-10EL8mm-2m-50-Ohm-Yagi.dwg, 435MHz-10EL8mm-2m-50-Ohm-Yagi.stl, Boom-cap.stl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]
2015-03-08 Add source file and binary for homing ring.
    [homing_ring.fcstd, homing_ring.stl]
2015-03-08 Modified axis gear ring in order to reduce friction.
    [axis_gear_spacer.fcstd, axis_gear_spacer.stl]
2015-03-08 Optimizing sensor holder for printability.
    [homing_sensor_holder.fcstd, homing_sensor_holder.stl]
2015-03-11 Add 3D printed cable hook to manage cables inside box
    [cable_hook.fcstd, cable_hook.stl]
2015-03-11 Modify axis_bushing to be able to hold 2 ISO 3601 Size:026 o-rings on each side (for the 32mm diameter tube) to prevent water from licking in the box.
    [axis_bushing.fcstd, axis_bushing.stl]
2015-04-14 Cleanup antennas repository.
    [145MHz-6-Element-2m-50-Ohm-Yagi.dwg, 145MHz-6-Element-2m-50-Ohm-Yagi.stl, 145MHz-6-Element-cap.stl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]
2015-05-08 First release of 4:1 balun PCB
    [four-to-one-balun.kicad_pcb, four-to-one-balun.sch]
2015-05-08 four-to-one-balun: Center schematic to page frame
    [four-to-one-balun.sch]
2015-05-09 Fix connector obstruction to antenna elements
    [four-to-one-balun.kicad_pcb, four-to-one-balun.sch]
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2015-06-13 nec2: Radiation pattern, gain and SWR charts for SatNOGS 6-element Yagi-Uda antenna
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2015-06-13 nec2: Add GNU octave calculator and NEC2 file for 10-element Yagi/Uda UHF antenna
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2015-09-01 Remove 'Balun' directory; four-to-one-balun has its own repository now at https://github.com/satnogs/four-to-one-balun/
    [four-to-one-balun.kicad_pcb, four-to-one-balun.sch]
2016-02-23 Designs for UHF Helical antenna in 434 MHz - 8 turns
    [Helical-434-6radialBase.dxf, Helical-434-8.xls, Helical-434-CooperTriangle.dxf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]
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2017-11-13 Incorporate versions in directory names
    [Helical-434-6radialBase.dxf, Helical-434-8.xls, Helical-434-CooperTriangle.dxf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]
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
